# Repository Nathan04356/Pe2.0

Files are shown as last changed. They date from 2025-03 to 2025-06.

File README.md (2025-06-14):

# PE2 - Nathan - Jonas

Wij maakten voor practice enterprise 2 een autonome robot stofzuiger. Deze kan navigeren via infraroodsensoren en een bumper met drukcontacten. Via een drukknop kan de stofzuiger navigeren naar zijn laadstation. Het laadstation is uitgerust met infrarood LEDs waarvan het patroon wordt opgevangen door de IR-receiver op de stofzuiger.

Hardware<br/>
-Schema's en PCB's zijn te vinden onder /Documenten<br/>
-Altium project van zowel stofzuiger als laadstation is terug te vinden in de map /Altium<br/>
-Datasheets zijn per PCB geordend in de map /Datasheets<br/>
Software<br/>
-Code van stofzuiger en laadstation is terug te vinden onder /Documenten<br/>
-STM project van zowel stofzuiger als laadstation is terug te vinden in de map /STM<br/>
Extra<br/>
-Extra info over de IR-sensoren (metingen)<br/>
-Volledige componentenlijst<br/>
Videos<br/>
-Video van gewone werking (stofzuiger.mp4)<br/>
-Video van naar dock te rijden (docking.mp4)<br/>
Verslag en PPT zijn terug te vinden in de root /<br/>

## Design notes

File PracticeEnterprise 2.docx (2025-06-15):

# Practice Enterprise 2:

# Autonome robot stofzuiger

GIT REPO: https://github.com/Nathan04356/PE2.0

# 1. Voorwoord (word of thanks)

Wij willen graag onze dank uiten aan onze leerkrachten die ons zo goed geholpen hebben. Namelijk meneer Dams en meneer Adriaensens.

# 2. Hoe het project gerealiseerd is.

Voor ons project kozen we ervoor om een autonome robotstofzuiger te maken. We begonnen met na te denken over welke functies het toestel moest hebben, zoals zelfstandig kunnen rijden, obstakels vermijden en stof opzuigen. Op basis daarvan besloten we welke onderdelen en modules we nodig hadden.

We maakten eerst een blokschema om een overzicht te krijgen van alle onderdelen en hoe ze met elkaar verbonden moesten worden. Daarna zijn we gestart met het tekenen van het elektrisch schema en het ontwerpen van de printplaat. Dit deden we met behulp van Altium Designer.

Toen de printplaat klaar was, konden we die bestellen en de componenten solderen zodra alles geleverd was.

Voor de programmatie gebruikten we een STM32L053C8T6 microcontroller. We schreven het programma in C, waarbij we de basisfunctionaliteiten van de robot implementeerden, zoals sturen, obstakels detecteren en autonoom bewegen.

# 3. Projectvoorstel

Ons project voorstel is het maken van een autonome robot stofzuiger.

Wij kiezen als centrale punt STM32L053C8T6, die we programeren met STM32CubeProgrammer.

Wij maken 2 PCB’s , één pcb voor de robotsofzuiger en één die als laadstation zal dienen. Wij gebruiken de AU-24.000MBE-T kristal als externe oscillator om een stabiele klok van 24 MHz te voorzien voor de STM32-microcontroller. Voor het programmeren en debuggen gebruiken wij de STLINK-V3MINIE, die via SWD met de microcontroller communiceert.

We gebruiken een lipo batterij van 3.7 v die regelen wij ook naar 3.3 volt om dingen zoals de µcontroller van juiste voeding te voorzien.

Voor de motoren aan te sturen gebruiken we een motor driver (TB6612FNG).

De TB6612FNG stuurt twee DC-motoren aan via een STM32 door per motor de draairichting te bepalen met IN1/IN2 en de snelheid met een PWM-signaal. De driver werkt op 3.3 V logica, heeft een aparte motorvoeding en wordt geactiveerd via de STBY-pin. Ideaal voor compacte, efficiënte robotbesturing.

Wij gebruiken de GP2Y0A21YK0F IR-afstandssensor om obstakels te detecteren. Deze sensor werkt op basis van reflectie van infrarood licht en geeft een analoge spanning die omgekeerd evenredig is met de afstand tot een object. Hij is betrouwbaar voor afstanden tussen ongeveer 10 en 80 cm en wordt via een ADC-ingang van de STM32 uitgelezen. Deze werkt op 5 volt daarmee gebruiken wij een boost converter om van de batterij spanning 3.7v naar 5 v te gaan.

Wij gebruiken eenvoudige mechanische drukcontacten om botsingen te detecteren. Wanneer de voorkant van de robot een obstakel raakt, wordt het contact gesloten en ontvangt de microcontroller een digitaal signaal. Hierdoor kan de robot meteen reageren, bijvoorbeeld door te stoppen of van richting te veranderen. Deze drukcontacten dienen als extra beveiliging naast de IR-sensoren.

Verder willen wij ook een laadstation maken waar de robot stofzuiger zal moeten terug kunnen keren.

Het laadstation maakt gebruik van de BQ24092, een slimme laadchip die een 1-cel Li-ion batterij veilig oplaadt via een standaard 5V micro-USB of VBUS-ingang. Zodra je een oplader aansluit, detecteert de chip dit en laat hij een LED branden via de PG-pin. Als er ook een batterij is aangesloten, start het laadproces en gaat een LED branden via de CHG-pin. Wanneer de batterij volledig is opgeladen, stopt de chip automatisch met laden en gaat de LED uit. De batterij is beschermd tegen overladen en ontladen dankzij een aparte beveiligingschip. Zo zorgt het laadstation automatisch voor veilig en efficiënt opladen.

# 4. Gantt chart

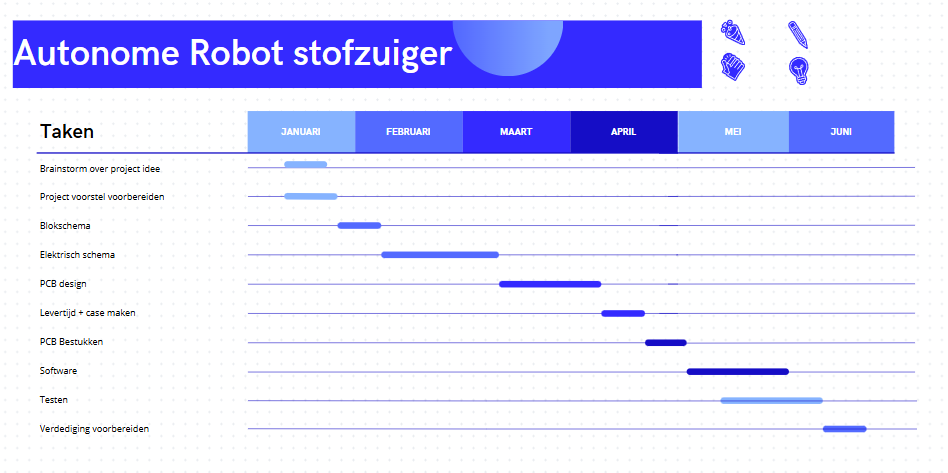
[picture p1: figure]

# 5. Problemen en oplossingen

## 5.1. Voeding

We waren van plan om één 18650-batterij van 3.7V te gebruiken, maar uiteindelijk bleek de stroom die de batterij kan leveren niet hoog genoeg te zijn om de motoren en de stofzuiger tegelijk te laten werken. Hierdoor zijn we moeten overschakelen naar drie batterijen. Als gevolg hiervan is de batterijspanning ook hoger dan de 5V die we nodig hebben voor de IR-sensoren, daardoor hebben we een 5V regelaar gebruikt om de hogere spanning naar 5V te brengen. De boost converter is uit het circuit verwijderd.

## 5.2. Laadstation

Als gevolg van het vorige probleem kan het laadstation niet gebruikt worden omdat het geen drie cellen kan opladen. Het laadstation is wel getest en werkt voor één cel, er zijn contacten voorzien op het station. De contacten op de robotstofzuiger zijn niet voorzien omdat we het laadstation toch niet kunnen gebruiken.

## 5.3. Auto-docking

Op het schema van stofzuiger deel 1 is een spanningsdeler voorzien om het batterijniveau op te meten via de ADC en aan de hand hiervan onder een bepaald niveau terug te rijden naar het station. Deze was uitgerekend voor één cel en is niet meer in gebruik voor drie cellen op dit moment. Weerstand R24 is niet aanwezig op de pcb.

## 5.4. Grond connectie usb

De grond is niet aangesloten op de usb-connector van het laadstation op het schema, waardoor het station eerst geen voeding kreeg. Dit is opgelost door deze aan een naburige grond te solderen.

## 5.5. Polarisatie charge led

De LED op de CHG uitgang van het laadstation staat fout gepolariseerd in het schema, deze is omgedraaid op de pcb.

## 5.6. Boost converter

We gebruikten eerst de TPS61023DRLR boost converter, maar bij het testen bleek dat deze voor kortsluiting zorgde en hebben we deze vervangen door een externe boost converter module. Door het bovenstaand vermelde voedingsprobleem hebben we dan deze module nog een vervangen door een LM7805 regelaar.

# 6. Hardware documentatie

## 6.1 Blokschema

### 6.1.1 Stofzuiger

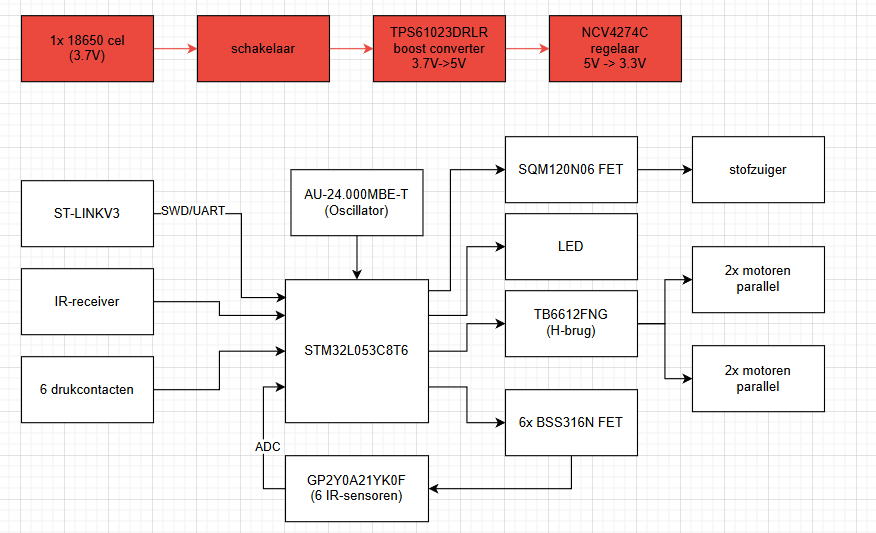
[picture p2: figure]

Het blokschema toont de opbouw van onze autonome robotstofzuiger. Een 3.7 V batterij voedt het systeem via een boost converter en spanningsregelaar. De STM32L053C8T6 microcontroller stuurt de motoren, stofzuiger en LED aan, en ontvangt signalen van IR-sensoren en drukcontacten. Een externe oscillator voorziet een stabiel kloksignaal, en programmering gebeurt via de STLINK-V3MINIE. Alles werkt samen om autonoom te navigeren en obstakels te vermijden.

### 6.1.2 Laadstation

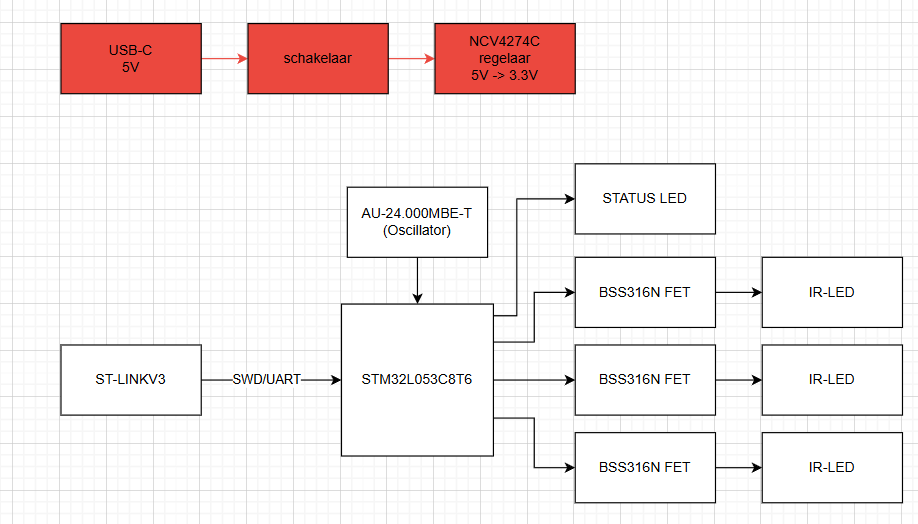
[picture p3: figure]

Dit blokschema toont een vereenvoudeld systeem voor het aansturen van IR-LEDs. De voeding gebeurt via een USB-C aansluiting van 5 V, die via een schakelaar en een NCV4274C spanningsregelaar wordt omgezet naar 3.3 V. De STM32L053C8T6 microcontroller vormt de centrale besturing, aangestuurd door een externe oscillator van 24 MHz. Programmeren gebeurt via ST-LINKV3 via SWD/UART. De microcontroller stuurt drie BSS316N MOSFETs aan die elk een IR-LED schakelen. Daarnaast wordt een status-LED aangestuurd voor visuele feedback.

## 6.2 Schema’s

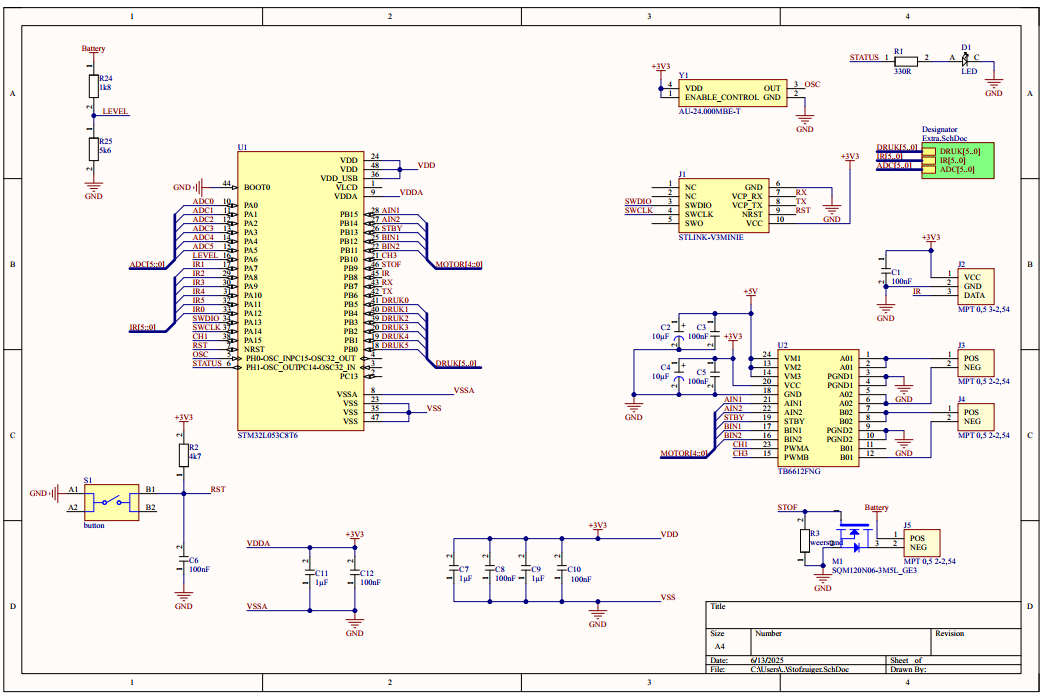
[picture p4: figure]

### 6.2.1 Stofzuiger deel 1

### 6.1.1 Stofzuiger deel 2

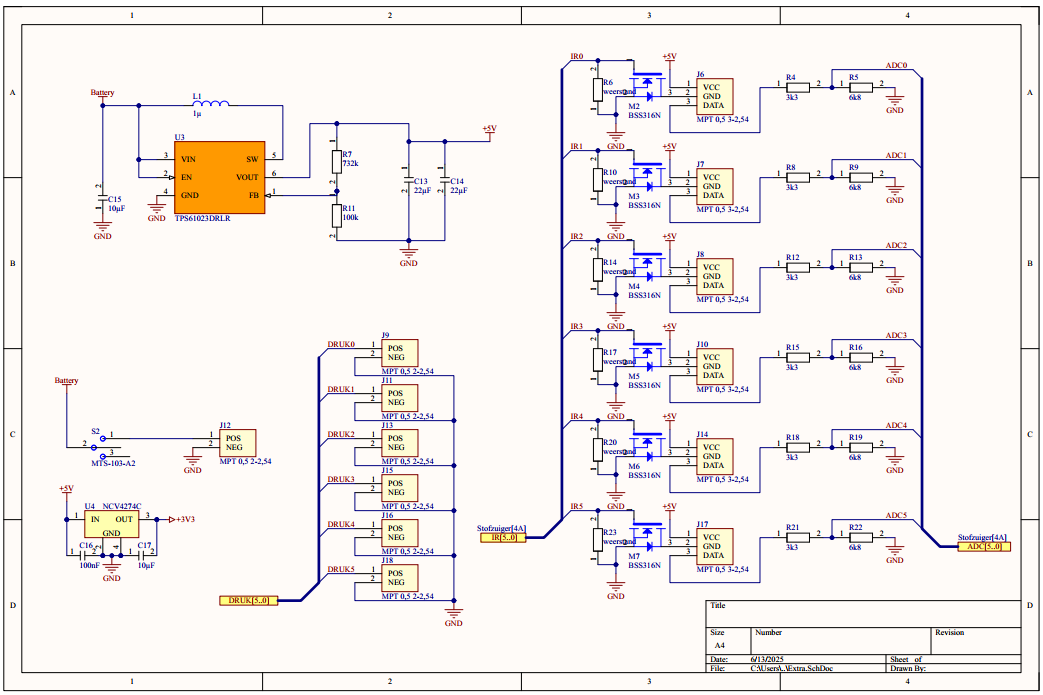
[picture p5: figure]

### 6.1.2 Laadstation deel 1

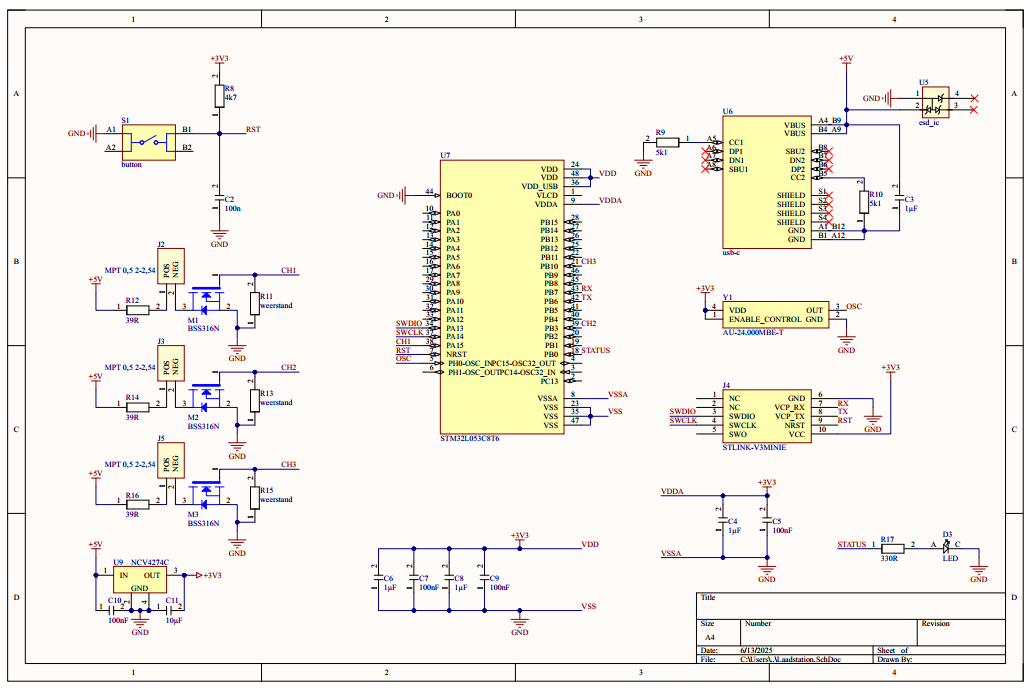
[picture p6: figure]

### 6.1.3 Laadstation deel 2

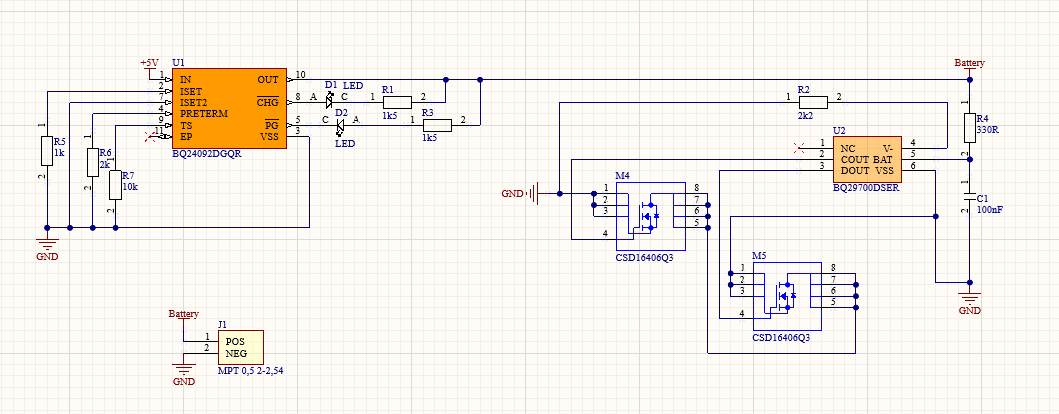
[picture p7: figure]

## 6.1 Component lay-out

### 6.1.1 Stofzuiger top-layer

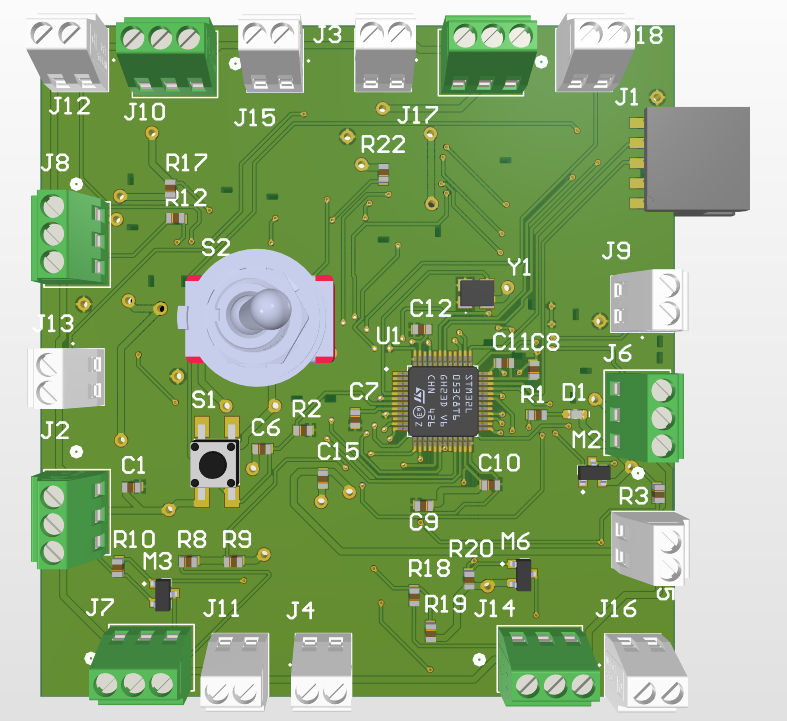
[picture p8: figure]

### 6.1.2 Stofzuiger bottom-layer

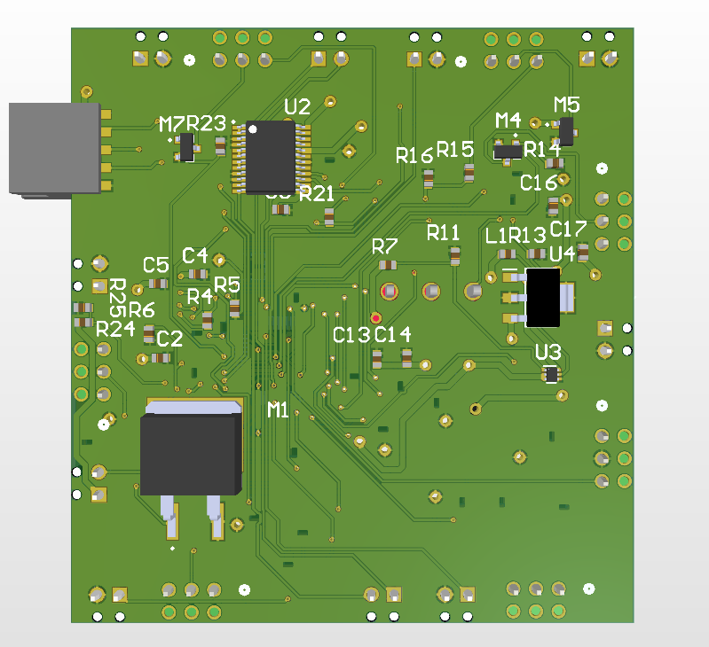
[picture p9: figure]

### 6.1.3 Laadstation

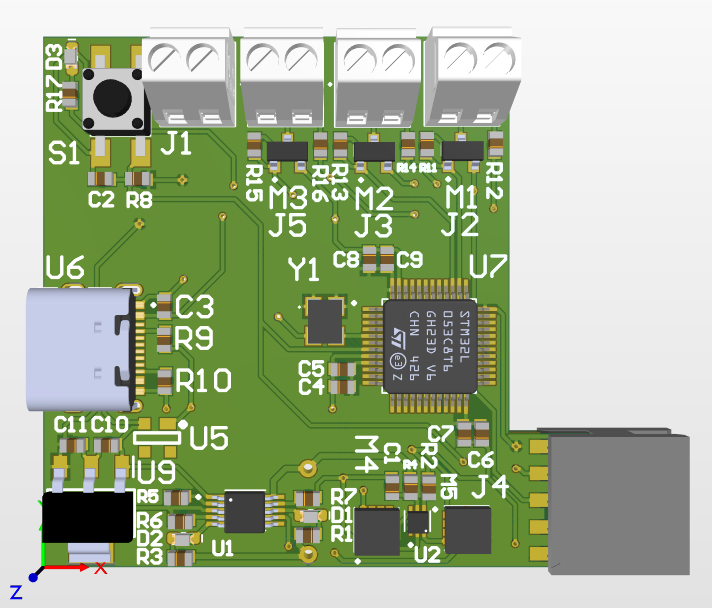
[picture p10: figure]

## 6.2 PCB lay-out

### 6.2.1 Stofzuiger top-layer

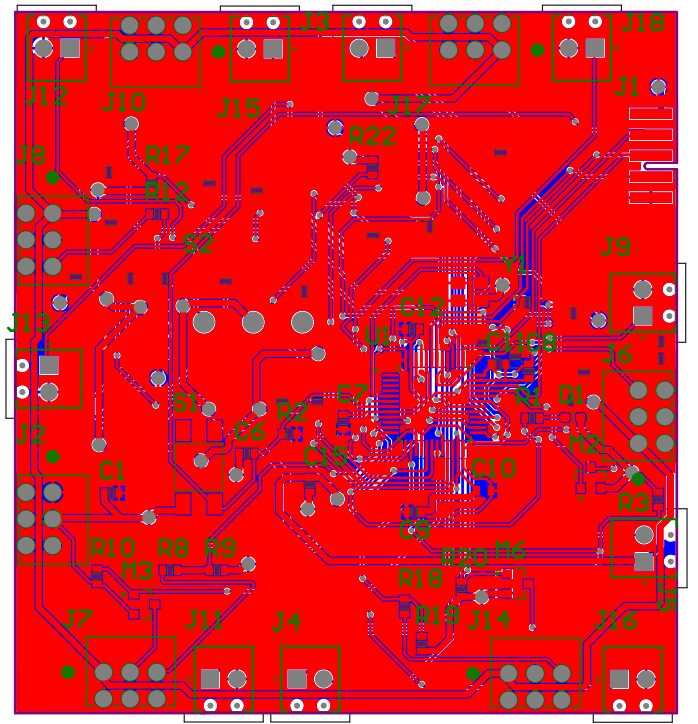
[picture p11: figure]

### 6.2.2 Stofzuiger bottom-layer

### 6.2.3 Laadstation

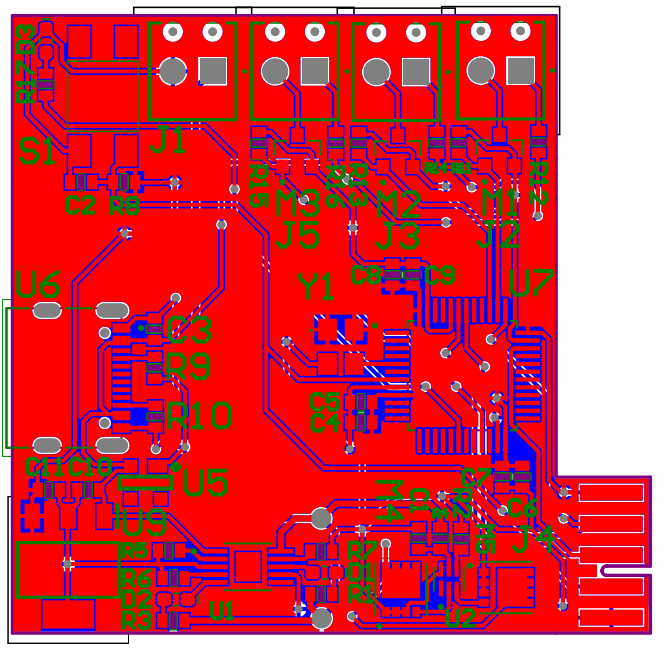
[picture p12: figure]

## 6.3 Materialen

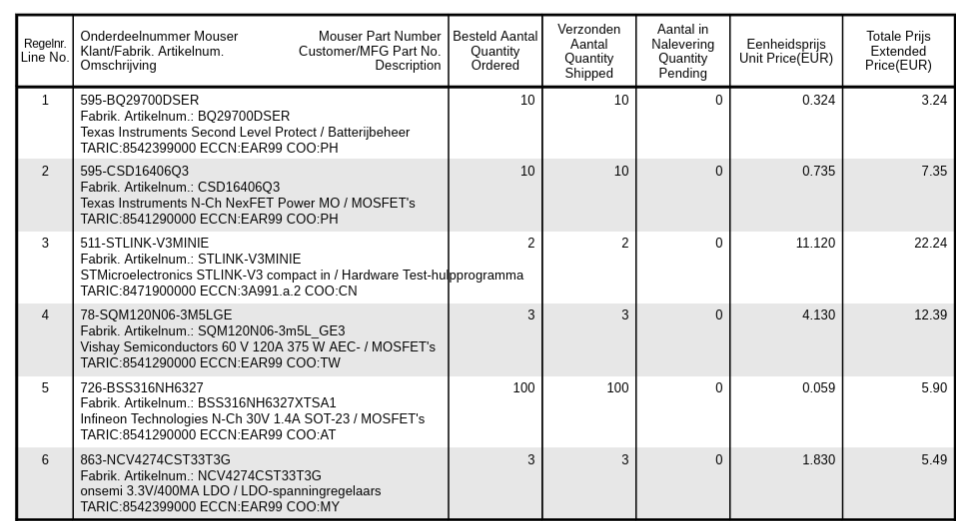
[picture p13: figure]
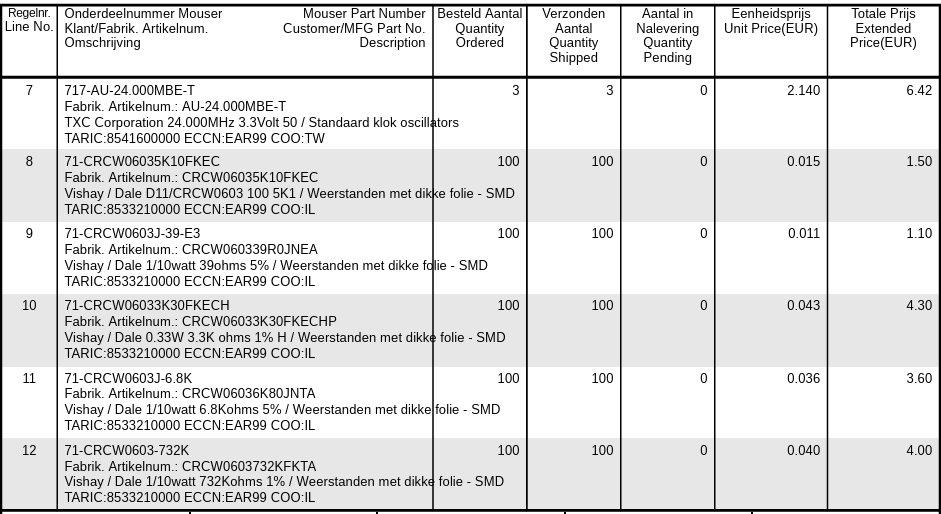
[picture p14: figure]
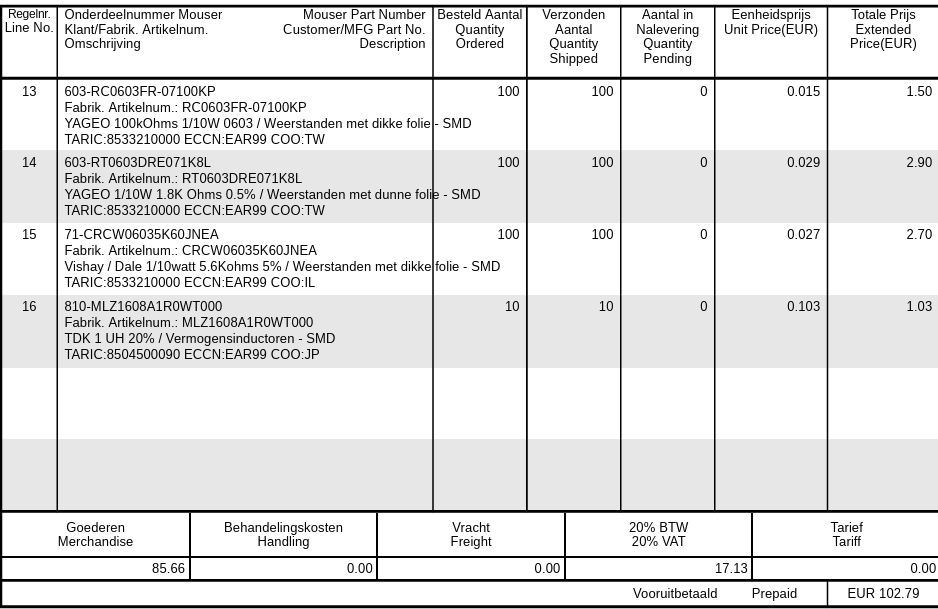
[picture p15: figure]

## 6.4 Datasheets

Datasheet STM32l053c8t6 (https://www.st.com/resource/en/datasheet/stm32l053c8.pdf)

Datasheet TB6612FNG (Dual H-bridge motordriver) (https://toshiba.semicon-storage.com/info/docget.jsp?did=10812&prodName=TB6612FNG)

Datasheet GP2Y0A21YK0F (IR-afstandssensor) (https://global.sharp/products/device/lineup/data/pdf/datasheet/gp2y0a21yk_e.pdf)

Datasheet AU-24.000MBE-T (24 MHz kristaloscillator) (https://abracon.com/Resonators/AU-MBE.pdf)

Datasheet STLINK-V3MINIE (Programmer/debugger) (https://www.st.com/resource/en/user_manual/dm00716816.pdf)

Datasheet Vergelijkbare mechanische drukknop (Omron D2F-type) (https://omronfs.omron.com/en_US/ecb/products/pdf/en-d2f.pdf)

Datasheet SQM120N06-3M5L_GE3 (Mosfet aan uit schakelen stofzuiger)

(https://www.vishay.com/docs/63814/sqm120n06-3m5l.pdf)Datasheet TPS61023DRLR (Boost converter) (https://www.ti.com/lit/ds/symlink/tps61023.pdf)

Datasheet NCV4274C(LDO 3.3 v) (https://www.onsemi.com/pdf/datasheet/ncv4274c-d.pdf)

Datasheet BSS316N (https://www.infineon.com/dgdl/Infineon-BSS316N-DS-v02_03-EN.pdf?fileId=db3a304330f686060130ff7ee4b07f16)

Datasheet BQ24092DGQR (https://www.ti.com/lit/ds/symlink/bq24090.pdf)

Datasheet BQ29700DSER (https://www.ti.com/lit/ds/symlink/bq2970.pdf?ts=1749963523532)

# 7. Software documentatie

## 7.1 Flowchart

### 7.1.1 Stofzuiger

#### 7.1.1.1 Main

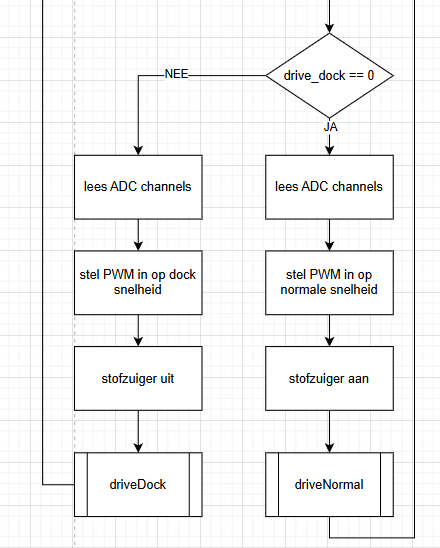
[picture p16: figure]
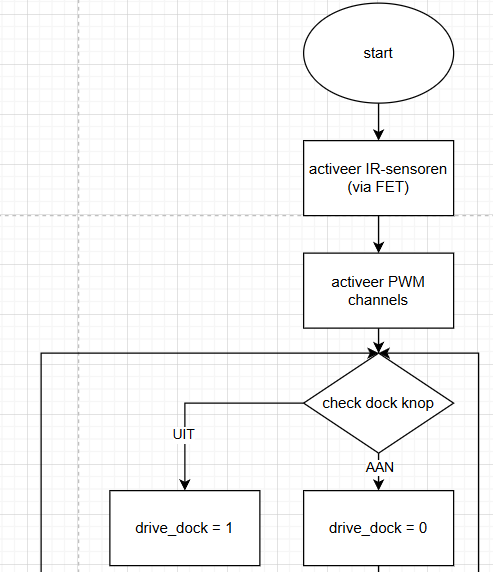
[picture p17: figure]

De stofzuiger zal eerst de nodige IR-sensors activeren en de PWM channels voor de motoren. Hierna wordt de drukknop op de robot gechecked om te beslissen of er naar dock wordt gereden of niet.

Indien de drukknop niet was ingedrukt worden de ADC channels uitgelezen van de IR-sensoren en wordt de PWM op de maximale snelheid ingesteld. De stofzuiger gaat aan en de functie voor het vermijden van opstakels wordt opgeroepen. Als de knop wel was ingedrukt worden de ADC-channels ook gelezen, maar de PWM wordt nu ingesteld op een lagere dock snelheid en de stofzuiger gaat uit.

De 12-bit waarden van de ADC met bijhorende afstand wordt weergeven in volgende grafiek.

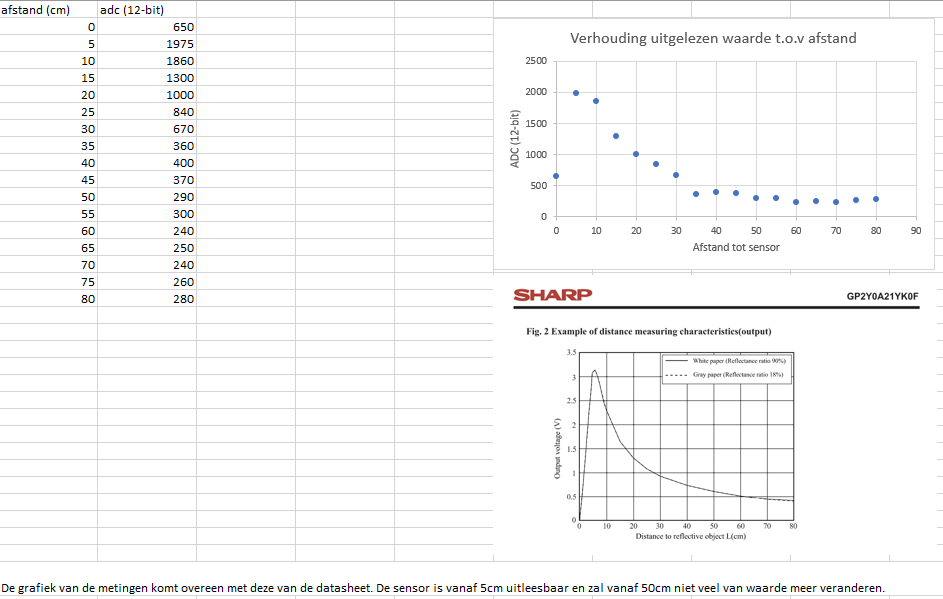
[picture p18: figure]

Hoe groter de ADC-waarde hoe dichter de sensor bij een obstakel is, tenzij te dicht.

#### 7.1.1.2 driveNormal

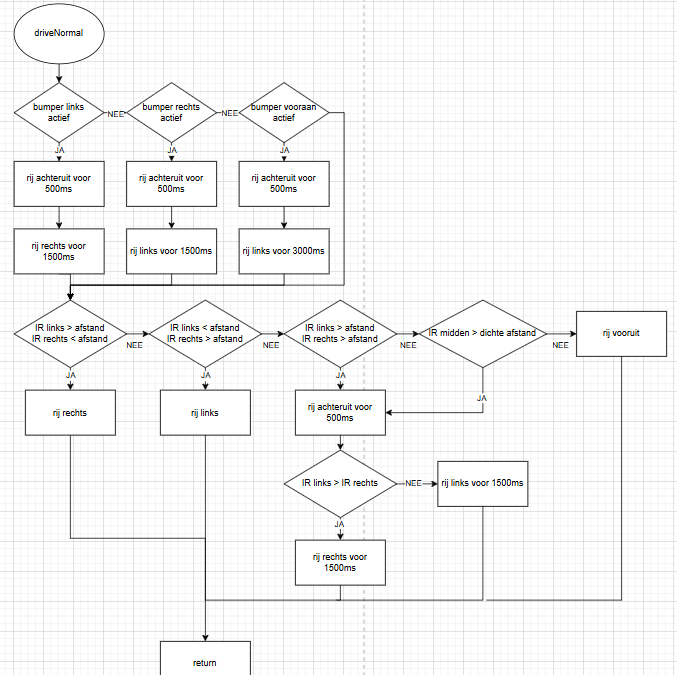
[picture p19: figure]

De obstakel functie bekijkt eerst of er een bumper actief is, indien dit het geval is wordt er achteruitgereden en gedraaid naar de gepaste richting. Daarna worden de afstanden van de IR-sensoren bekeken.

Indien linkse sensor te dicht is wordt er naar rechts gedraaid en omgekeerd bij de rechtse sensor. Als beide links en rechts te dicht zijn of midden veel te dicht wordt er achteruitgereden en afgedraaid naar de kant waar het meeste plaats is. Als geen enkele sensor te dicht komt rijdt de stofzuiger vooruit.

#### 7.1.1.3 driveDock

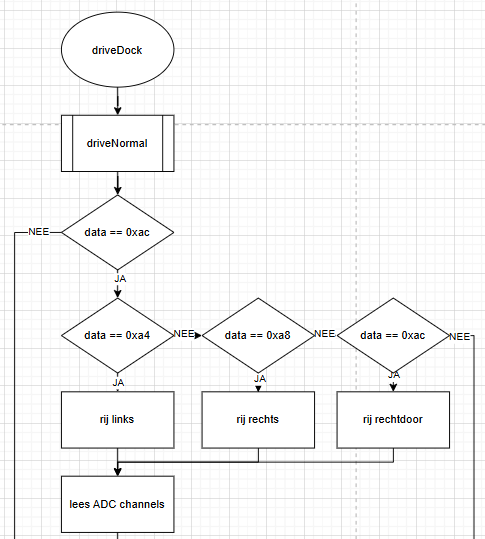
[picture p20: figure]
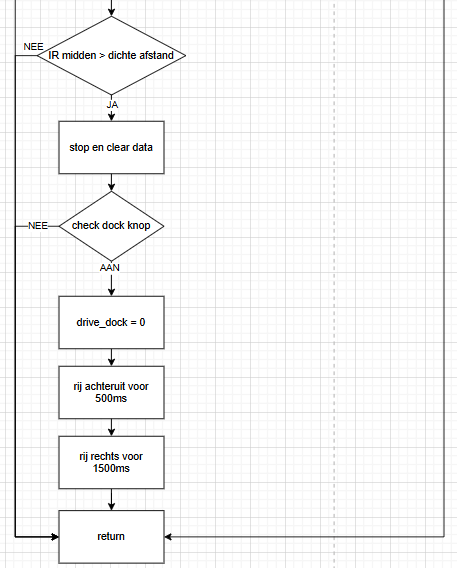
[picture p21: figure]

De ADC-waarden worden gebruikt om te navigeren in de vorig uitgelegde functie driveNormal. De stofzuiger gebruikt dan de data van de IR-receiver (komt vanuit interrupt zie later) om de rechte lijn vanaf het dock station te detecteren.

De linker IR-LED van het dock station stuurt 0xa8 en de rechter 0xa4, samen en dus in het midden is dit 0xac. Indien het midden is gevonden gebruikt de stofzuiger de IR-patronen om te navigeren.

Vervolgens worden de ADC-channels nog gemeten om te checken of de middenste sensor dicht genoeg bij het dock staat. Als deze dicht genoeg is stopt de stofzuiger en wacht deze op een signaal van de dock button. De knop wordt ingedrukt, de stofzuiger rijdt achteruit en naar rechts. Hij gaat terug in de normale modus.

#### 7.1.1.4 interrupt

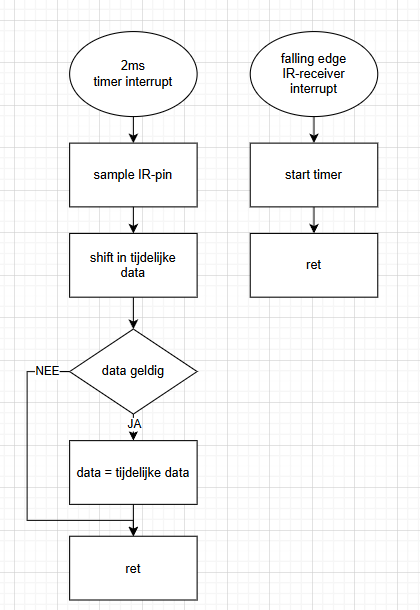
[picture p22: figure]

Het sampelen van de IR-LED data gebeurt via de IR-receiver. Deze geeft een actief laag signaal bij het ontvangen van 38kHz gemoduleerd licht. Er wordt op elke bit gesynchroniseerd door een external interrupt met falling edge detection te gebruiken op de IR-receiver output. Er wordt een timer gestart om in het midden van de bit te sampelen.

De data wordt vervolgens in een tijdelijk register geshift tot er geldige data is en deze beschikbaar is in het gebruikte data register.

### 7.1.2 Laadstation

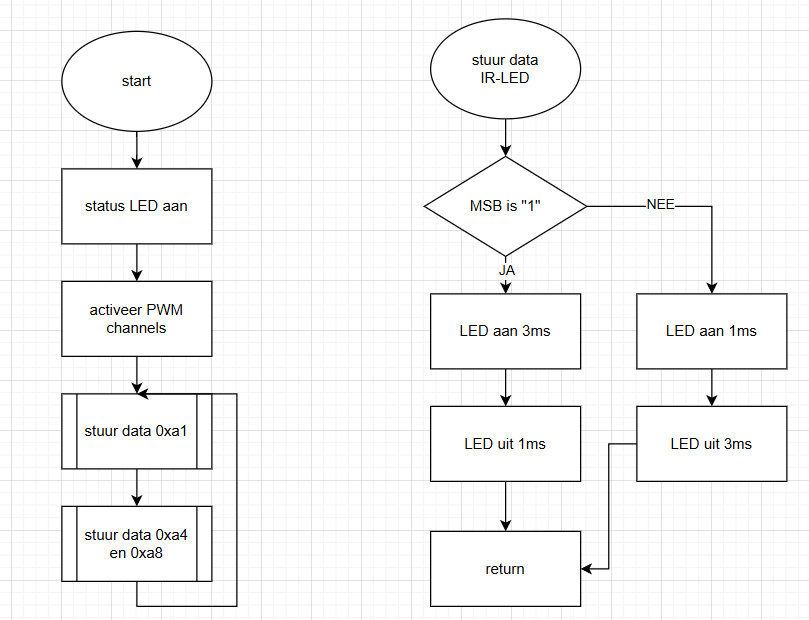
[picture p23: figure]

Het laadstation gebruikt een functie om één channel van een IR-LED op 38kHz te moduleren en data te versturen en een functie om dit te doen op twee channels. Voor de eenvoudigheid is hier rechts de functie voor één channel weergegeven.

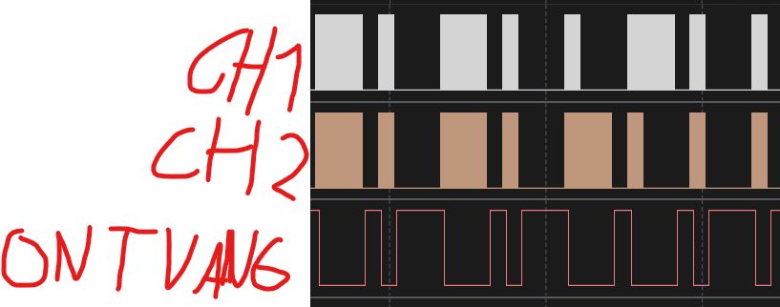
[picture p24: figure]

Indien er een ‘1’ moet worden verstuurd zal de led 3ms aan gaan en 1ms uit. Bij een ‘0’ zal de led 1ms aan gaan en 3ms uit. Hierdoor is er altijd een falling edge op de receiver om te hersynchroniseren. In bovenstaande figuur is CH1 aangestuurd met het patroon 0xa4 en CH2 met 0xa8. Als de ontvanger beide patronen tegelijk ziet komt er 0xac binnen.

# 8. Conclusie

Wij hebben met dit project een autonome robotstofzuiger ontwikkeld die zelfstandig kan navigeren en reageren op zijn omgeving. Door het gebruik van de STM32L053C8T6 microcontroller, IR-afstandssensoren en drukcontacten kan de robot obstakels detecteren en vermijden. De motoren worden efficiënt aangestuurd via een H-brug, en de stofzuigerfunctie wordt afzonderlijk geschakeld. Dankzij een combinatie van hardwareontwerp, printplaatontwikkeling en embedded software zijn we erin geslaagd om een functioneel en uitbreidbaar systeem te realiseren. Dit project heeft ons niet alleen technisch uitgedaagd, maar ook onze samenwerking en probleemoplossend denken versterkt.

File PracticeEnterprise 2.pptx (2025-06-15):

## Robotstofzuiger

Jonas blauwens / nathan vansevenant

## Inhoud

- Blokschema’s
- Schema’s
- PCB’s
- Software
- Problemen
- Conclusie

## Blokschema stofzuiger


## Blokschema laadstation


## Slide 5

Schema stofzuiger deel 1


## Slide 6

Schema stofzuiger deel 2


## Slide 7

Schema laadstation deel 1


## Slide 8

Schema laadstation deel 2


## PCB stofzuiger top


## PCB stofzuiger bottom


## PCB laadstation


## Software stofzuiger


## Software stofzuiger


## Software stofzuiger


## Software IR-LEDS en ontvanger


## Problemen

- Voeding en boost converter
- Opladen
- Auto-docking
- Grond connectie USB
- Polarisatie charge LED
- Boost converter module

## Conclusie


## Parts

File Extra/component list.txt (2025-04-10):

STM32L053C8T6 check 
NCV4274C	spanningsregaal  3.3 v check 3.3
tb6612fng x 3   H-brug check
SHarp GP2Y0A21YK0F x7	IR sensor check  
BQ24092DGQR check
BQ29700DSER check
KW11-3Z-B-1 x 10 botssesnor check 
micro N20 gear motor niet meer nodig
Phoenix contact x2 x10 check
Phoenix contact x3 x14 check genoeg?

STLINK-V3MINIE check

led check

SQM120N06-3M5L_GE3 check 
BSS316N check
MTS-103-A2 check
TB6612FNG check
TPS61023DRLR check
NCV4274C check
AU-24.000MBE-T check
CSD16406Q3 check
BQ24092DGQR check
BQ29700DSER check
esd_ic check
usb-c check

100nF check

22µF check
10µF check

100nF check
100n check
1µF check

3k3 check
6k8 check
732k check
100k check
1k8 check
5k6 check

spoel 1µ check

1k5 check
2k2 check
330R check
1k check
2k check
10k check
4k7 check 
5k1 check
39R check

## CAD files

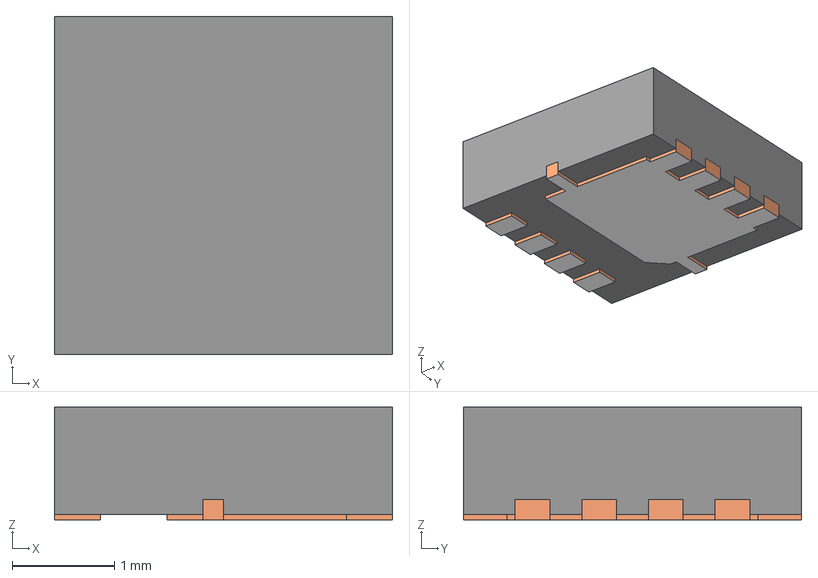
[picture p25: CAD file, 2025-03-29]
Altium/PE2/3D modellen/DQG0008A.stp
3.30 x 3.30 x 1.10 mm
BODY-SON
FRAME-DQG0008A
PIN1-ID

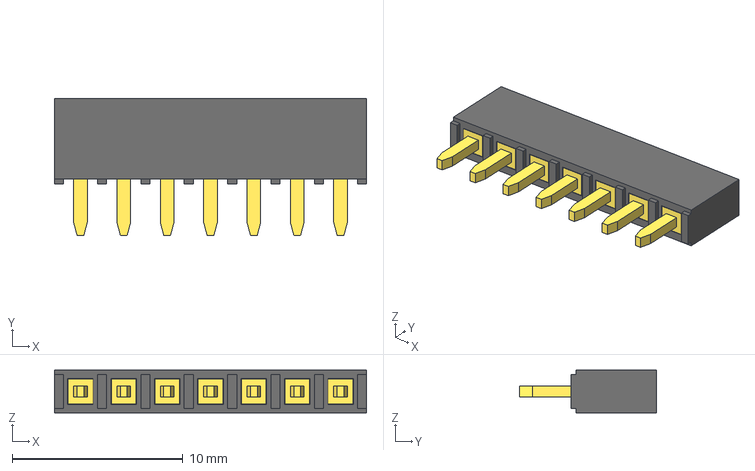
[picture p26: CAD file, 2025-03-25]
Altium/PE2/3D modellen/7-Pin Header - Female - 2.54mm.step
18.3 x 8.00 x 2.50 mm

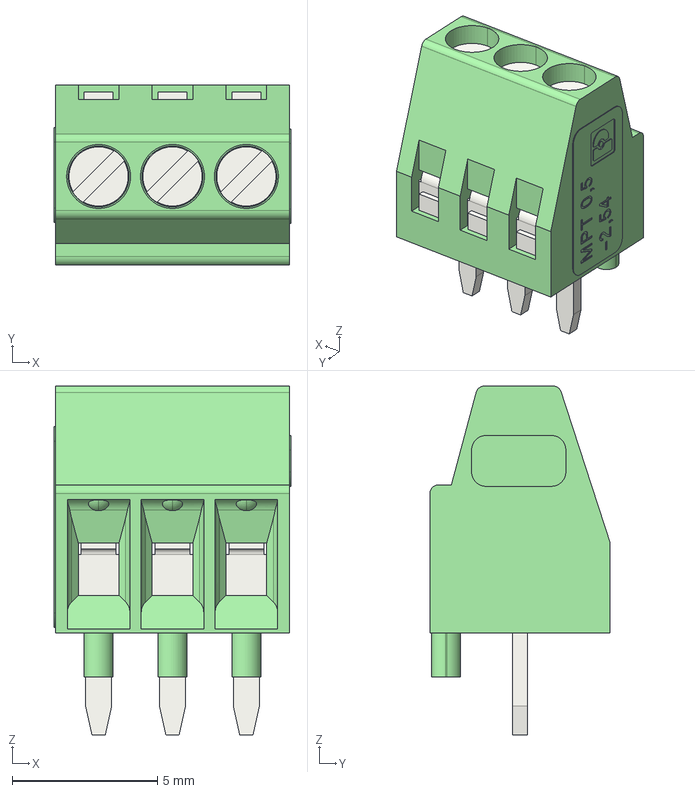
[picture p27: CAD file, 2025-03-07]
Altium/PE2/3D modellen/pxc_1725669_09_03_MPT-0-5-3-2-54_3D.stp
8.14 x 6.20 x 12.0 mm

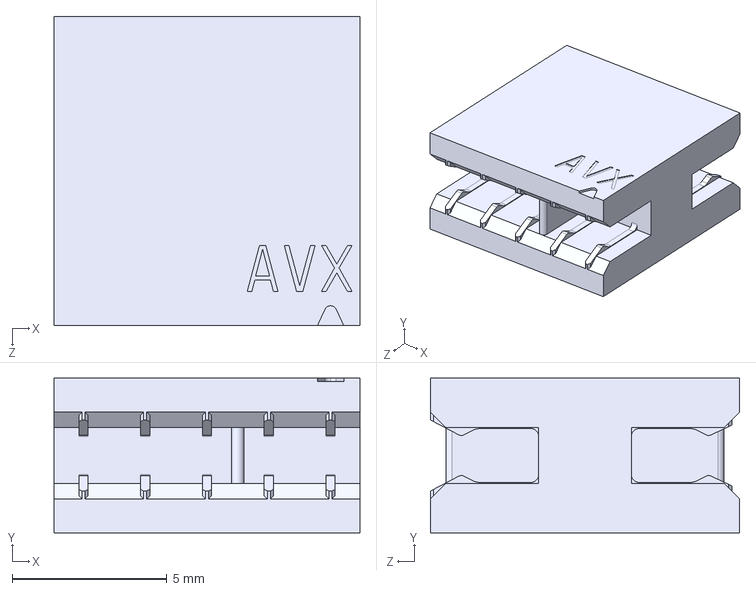
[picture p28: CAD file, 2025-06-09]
Altium/PE2/3D modellen/009159010061916.stp
9.90 x 5.00 x 10.0 mm

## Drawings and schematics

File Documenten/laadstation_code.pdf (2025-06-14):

main.c | Saturday, June 14, 2025, 2:55 PM

1 /* USER CODE BEGIN Header */
2 /**
3 ******************************************************************************
4 | * @file | : main.c
5 | * @brief | : Main program body
6 ****************************************************************************** 7 * @attention
8 *
9 * Copyright (c) 2025 STMicroelectronics.
10 * All rights reserved.
11 *
12 * This software is licensed under terms that can be found in the LICENSE file 13 * in the root directory of this software component.
14 * If no LICENSE file comes with this software, it is provided AS-IS.
15 *
16 ****************************************************************************** 17 */
18 /* USER CODE END Header */
19 /* Includes ------------------------------------------------------------------*/ 20 #include "main.h"
21
22 /* Private includes ----------------------------------------------------------*/ 23 /* USER CODE BEGIN Includes */
24 #include <stdio.h>
25 /* USER CODE END Includes */
26
27 /* Private typedef -----------------------------------------------------------*/ 28 /* USER CODE BEGIN PTD */
29
30 /* USER CODE END PTD */
31
32 /* Private define ------------------------------------------------------------*/ 33 /* USER CODE BEGIN PD */
34
35 /* USER CODE END PD */
36
37 /* Private macro -------------------------------------------------------------*/ 38 /* USER CODE BEGIN PM */
39 #define DUTY_VAL 14
40 /* USER CODE END PM */
41
42 /* Private variables ---------------------------------------------------------*/ 43 TIM_HandleTypeDef htim2;
44
45 UART_HandleTypeDef huart1;
46
47 /* USER CODE BEGIN PV */ 48
49 /* USER CODE END PV */
50
51 /* Private function prototypes -----------------------------------------------*/ 52 void SystemClock_Config(void);
53 static void MX_GPIO_Init(void);
54 static void MX_USART1_UART_Init(void);
55 static void MX_TIM2_Init(void);
56 /* USER CODE BEGIN PFP */
57 int _write(int, char *, int);
58 void stuurDataIrSolo (uint8_t);
59 void stuurDataIrDuo (uint8_t, uint8_t);
60 void stuurDataIrAll (uint8_t, uint8_t, uint8_t);
61 /* USER CODE END PFP */
62
63 /* Private user code ---------------------------------------------------------*/ 64 /* USER CODE BEGIN 0 */
| | Page 1

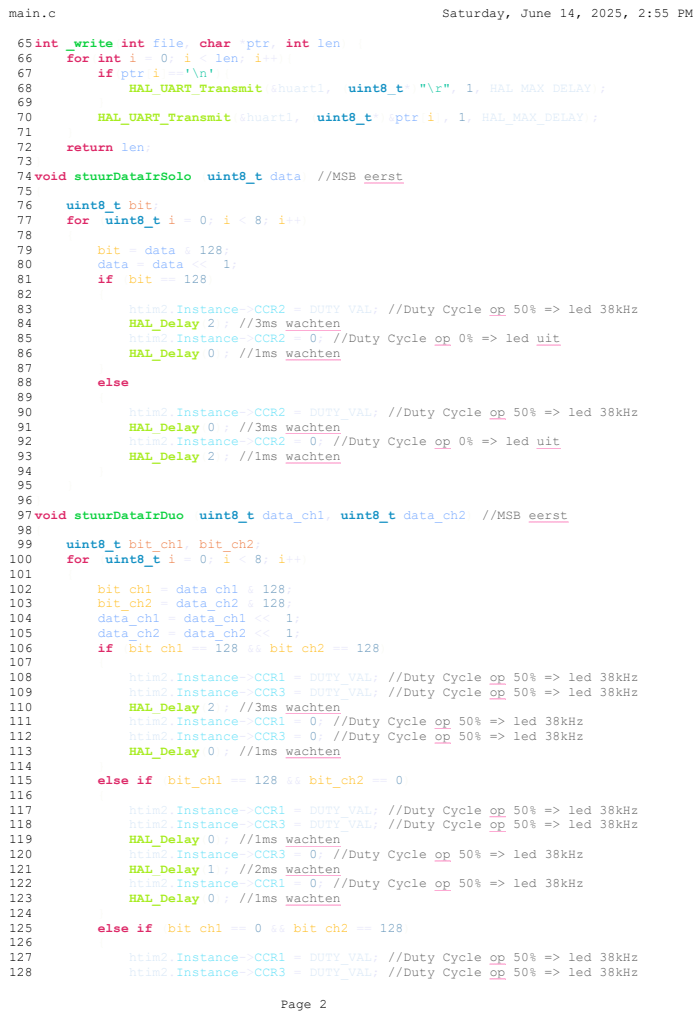
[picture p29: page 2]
main.c; Saturday, June 14, 2025, 2:55 PM; Page 2

65 int _write(int file, char *ptr, int len) {
66 for(int i = 0; i < len; i++){
67 if(ptr[i]=='\n'){
68 HAL_UART_Transmit(&huart1, (uint8_t*)"\r", 1, HAL_MAX_DELAY);
70 HAL_UART_Transmit(&huart1, (uint8_t*)&ptr[i], 1, HAL_MAX_DELAY);
72 return len;
74 void stuurDataIrSolo (uint8_t data) //MSB eerst
76 uint8_t bit;
77 for (uint8_t i = 0; i < 8; i++)
79 bit = data & 128;
80 data = data << 1;
81 if (bit == 128)
83 htim2.Instance->CCR2 = DUTY_VAL; //Duty Cycle op 50% => led 38kHz
84 HAL_Delay(2); //3ms wachten
85 htim2.Instance->CCR2 = 0; //Duty Cycle op 0% => led uit
86 HAL_Delay(0); //1ms wachten
88 else
90 htim2.Instance->CCR2 = DUTY_VAL; //Duty Cycle op 50% => led 38kHz
91 HAL_Delay(0); //3ms wachten
92 htim2.Instance->CCR2 = 0; //Duty Cycle op 0% => led uit
93 HAL_Delay(2); //1ms wachten
97 void stuurDataIrDuo (uint8_t data_ch1, uint8_t data_ch2) //MSB eerst
99 uint8_t bit_ch1, bit_ch2;
100 for (uint8_t i = 0; i < 8; i++)
102 bit_ch1 = data_ch1 & 128;
103 bit_ch2 = data_ch2 & 128;
104 data_ch1 = data_ch1 << 1;
105 data_ch2 = data_ch2 << 1;
106 if (bit_ch1 == 128 && bit_ch2 == 128)
108 htim2.Instance->CCR1 = DUTY_VAL; //Duty Cycle op 50% => led 38kHz
109 htim2.Instance->CCR3 = DUTY_VAL; //Duty Cycle op 50% => led 38kHz
110 HAL_Delay(2); //3ms wachten
111 htim2.Instance->CCR1 = 0; //Duty Cycle op 50% => led 38kHz
112 htim2.Instance->CCR3 = 0; //Duty Cycle op 50% => led 38kHz
113 HAL_Delay(0); //1ms wachten
115 else if (bit_ch1 == 128 && bit_ch2 == 0)
117 htim2.Instance->CCR1 = DUTY_VAL; //Duty Cycle op 50% => led 38kHz
118 htim2.Instance->CCR3 = DUTY_VAL; //Duty Cycle op 50% => led 38kHz
119 HAL_Delay(0); //1ms wachten
120 htim2.Instance->CCR3 = 0; //Duty Cycle op 50% => led 38kHz
121 HAL_Delay(1); //2ms wachten
122 htim2.Instance->CCR1 = 0; //Duty Cycle op 50% => led 38kHz
123 HAL_Delay(0); //1ms wachten
125 else if (bit_ch1 == 0 && bit_ch2 == 128)
127 htim2.Instance->CCR1 = DUTY_VAL; //Duty Cycle op 50% => led 38kHz
128 htim2.Instance->CCR3 = DUTY_VAL; //Duty Cycle op 50% => led 38kHz

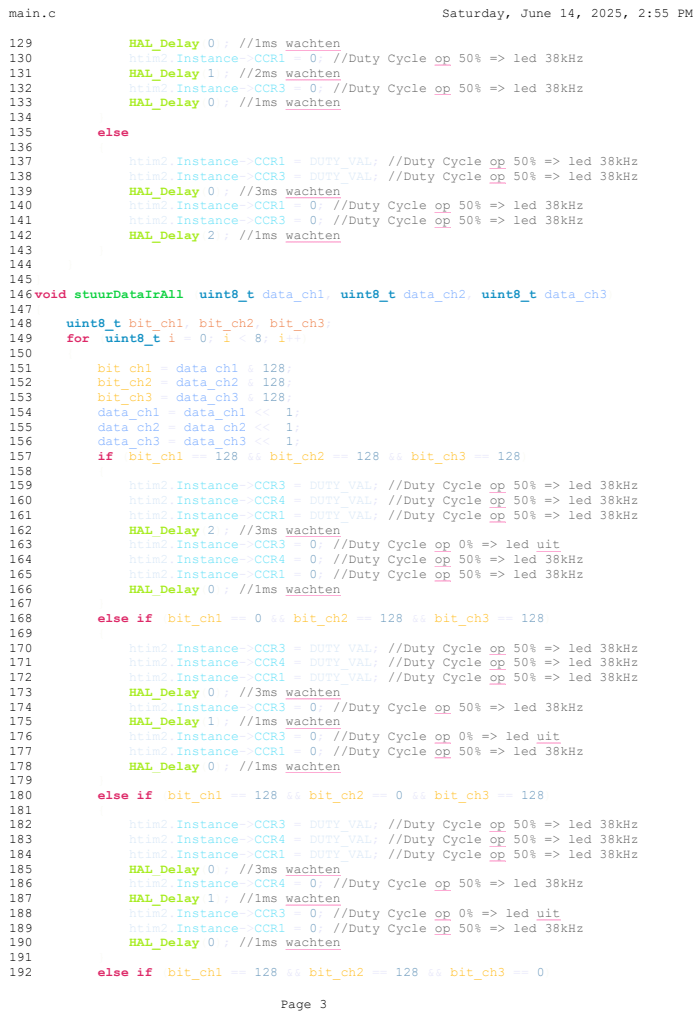
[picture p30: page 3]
main.c; Saturday, June 14, 2025, 2:55 PM; Page 3
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

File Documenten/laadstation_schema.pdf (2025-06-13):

4k7 2 1

# GND 2 1

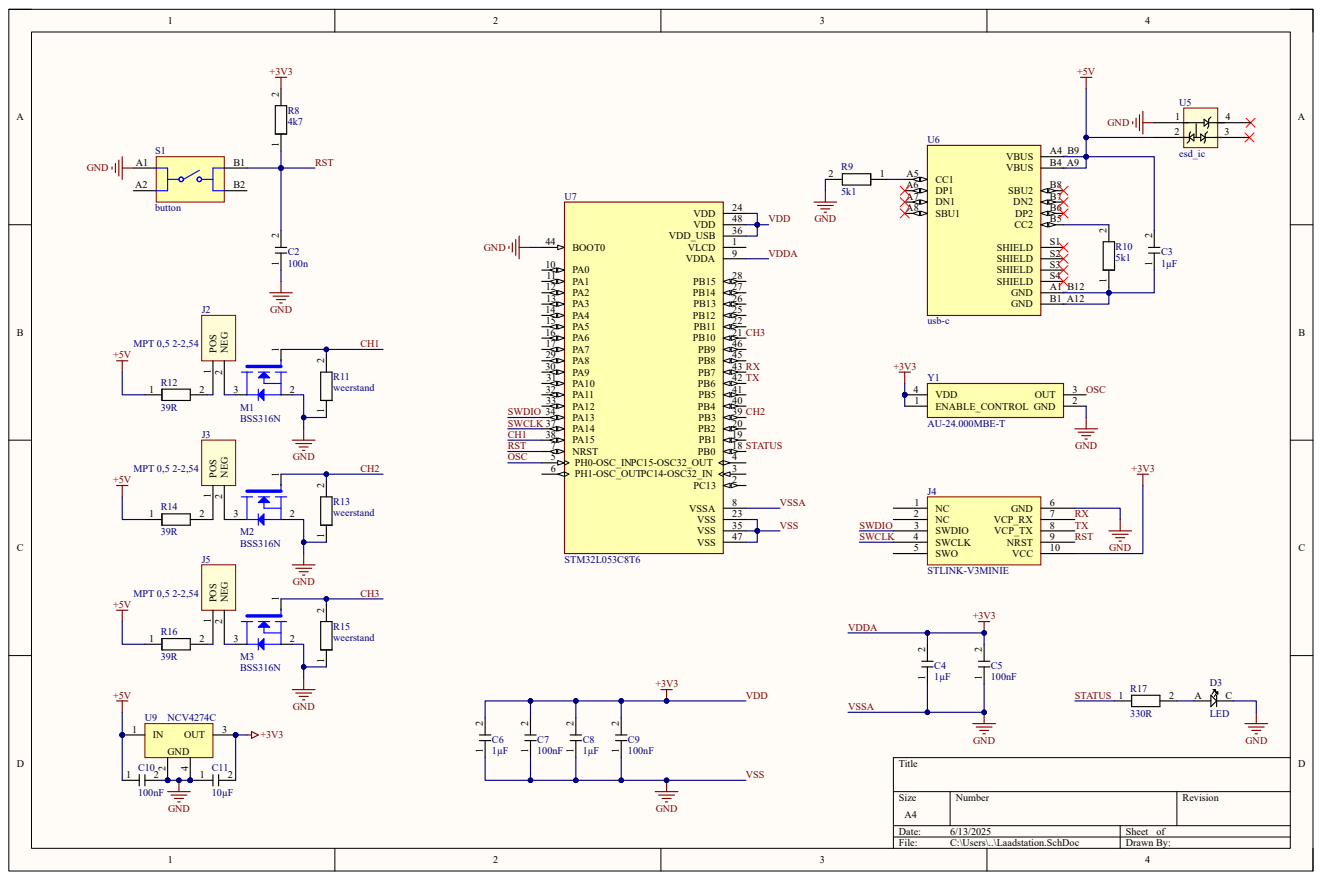
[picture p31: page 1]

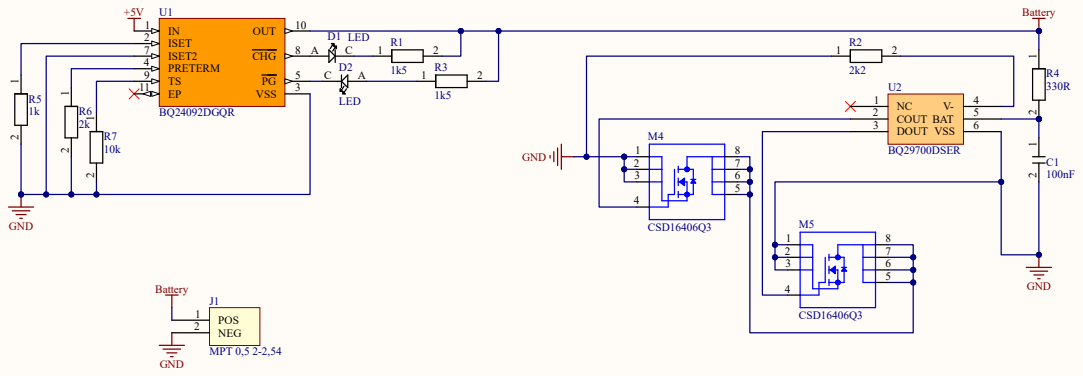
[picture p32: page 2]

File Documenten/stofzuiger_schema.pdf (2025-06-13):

IR[5..0] 2 1

1k8 1 2

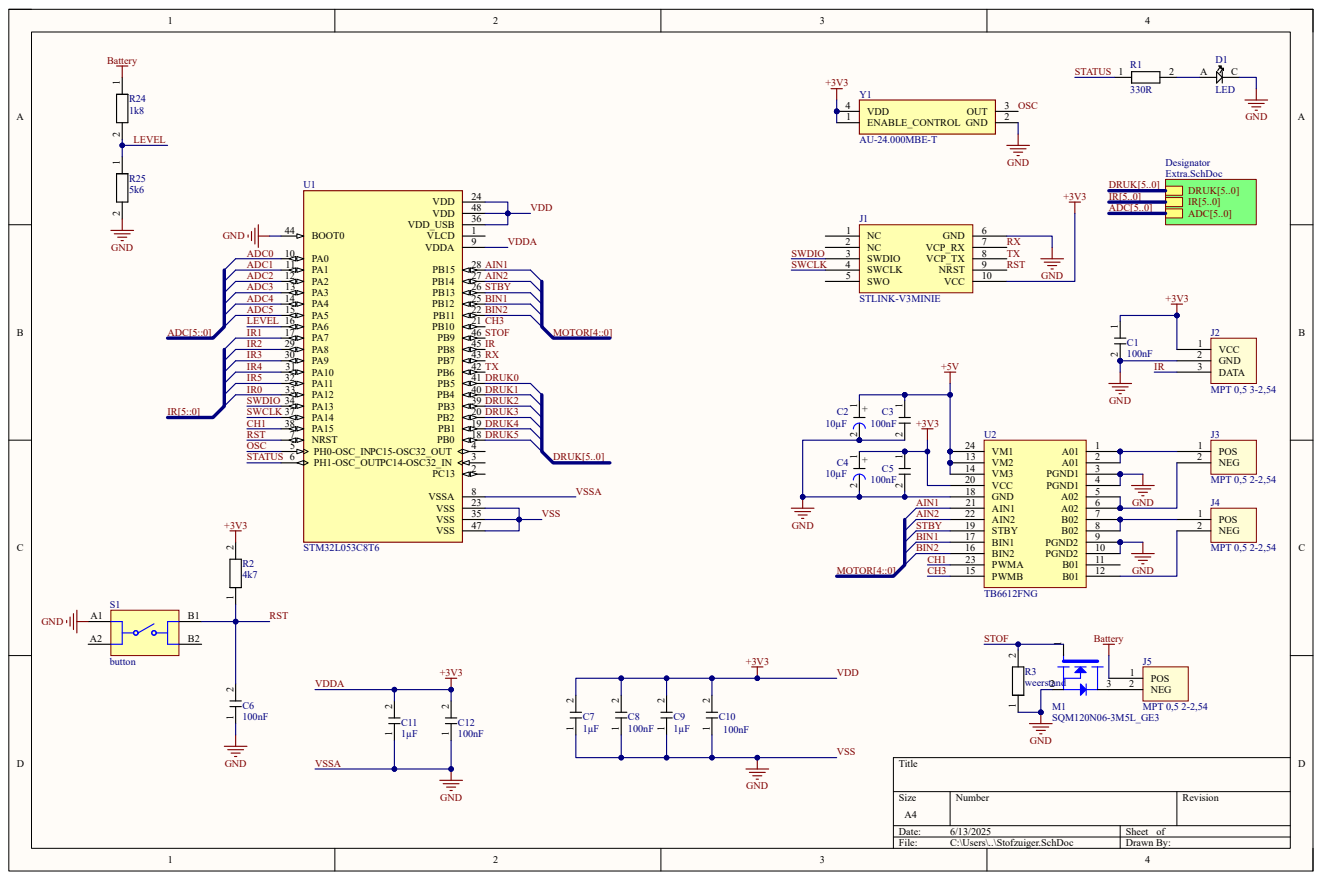
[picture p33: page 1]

732k 1 2

# GND ¹ 2

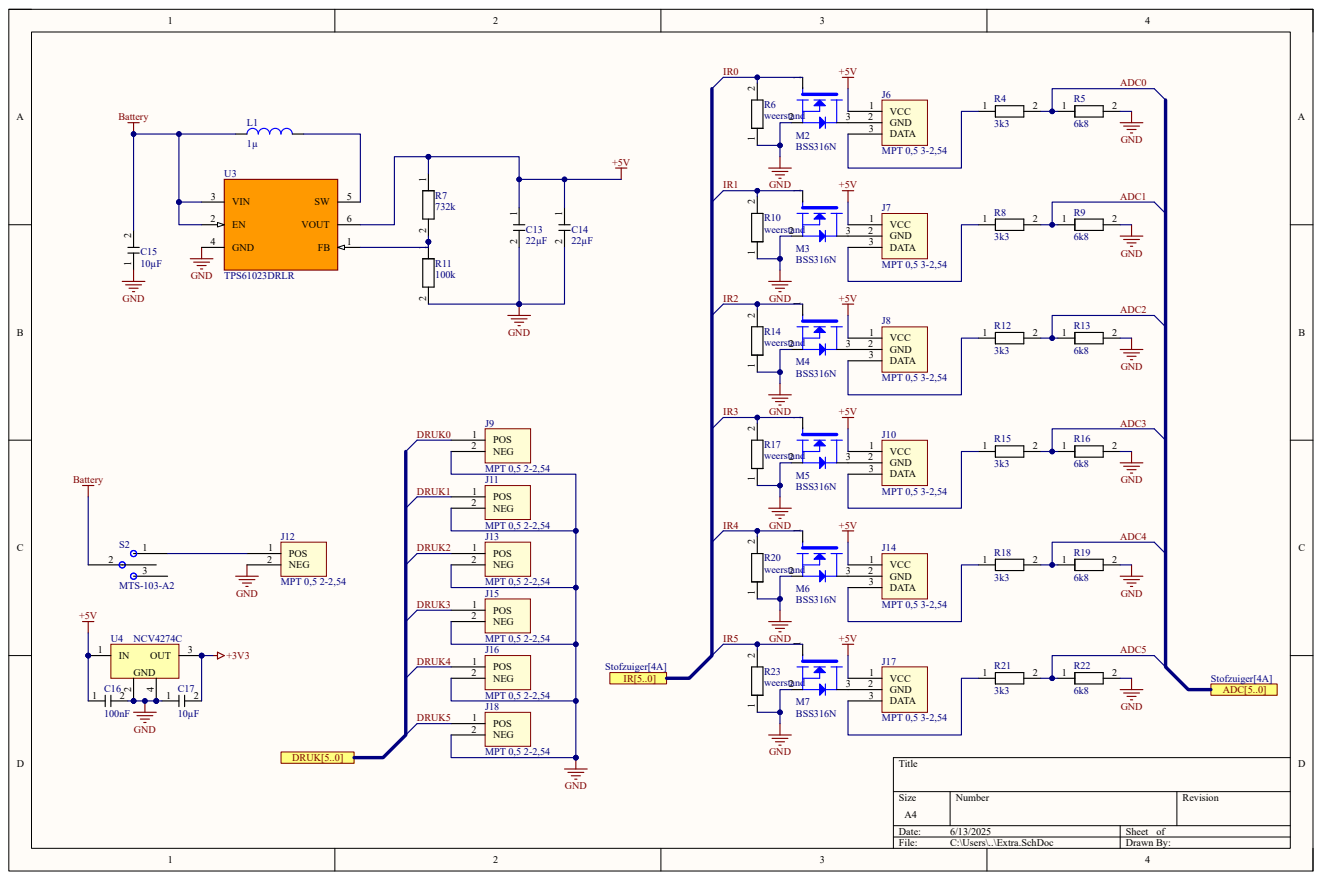
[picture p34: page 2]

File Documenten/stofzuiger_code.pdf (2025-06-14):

main.c | Saturday, June 14, 2025, 2:54 PM

1 /* USER CODE BEGIN Header */
2 /**
3 ******************************************************************************
4 | * @file | : main.c
5 | * @brief | : Main program body
6 ****************************************************************************** 7 * @attention
8 *
9 * Copyright (c) 2025 STMicroelectronics.
10 * All rights reserved.
11 *
12 * This software is licensed under terms that can be found in the LICENSE file 13 * in the root directory of this software component.
14 * If no LICENSE file comes with this software, it is provided AS-IS.
15 *
16 ****************************************************************************** 17 */
18 /* USER CODE END Header */
19 /* Includes ------------------------------------------------------------------*/ 20 #include "main.h"
21
22 /* Private includes ----------------------------------------------------------*/ 23 /* USER CODE BEGIN Includes */
24 #include <stdio.h>
25 /* USER CODE END Includes */
26
27 /* Private typedef -----------------------------------------------------------*/ 28 /* USER CODE BEGIN PTD */
29
30 /* USER CODE END PTD */
31
32 /* Private define ------------------------------------------------------------*/ 33 /* USER CODE BEGIN PD */
34
35 /* USER CODE END PD */
36
37 /* Private macro -------------------------------------------------------------*/ 38 /* USER CODE BEGIN PM */
39 #define VOORUIT (GPIOB->BSRR = 0xF800B000);
40 #define ACHTERUIT (GPIOB->BSRR = 0xF8006800);
41 #define LINKS (GPIOB->BSRR = 0xF800A800);
42 #define RECHTS (GPIOB->BSRR = 0xF8007000); 43 #define UIT (GPIOB->BSRR = 0xF8000000);
44 #define NORMAL_SPEED 255
45 #define DOCK_SPEED 145
46 #define IR_SENSOR_COUNT 3
47 #define IR_SENSOR_DISTANCE 1500
48 #define IR_MID_SENSOR_DISTANCE 2200 49 #define ACHTERUIT_DELAY 500
50 #define DRAAI_DELAY 1500
51 #define LANG_DRAAI_DELAY 3000
52 /* USER CODE END PM */
53
54 /* Private variables ---------------------------------------------------------*/ 55 ADC_HandleTypeDef hadc;
56
57 TIM_HandleTypeDef htim2;
58 TIM_HandleTypeDef htim6; 59
60 UART_HandleTypeDef huart1; 61
62 /* USER CODE BEGIN PV */ 63 uint8_t sample = 0;
64 uint8_t data = 0;
| | Page 1

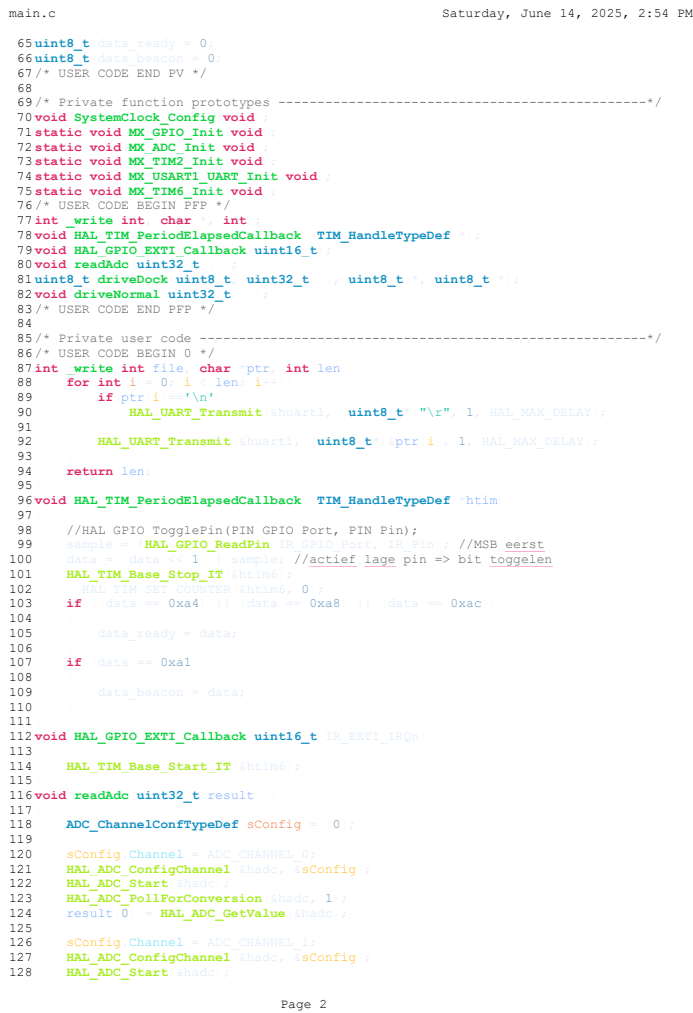
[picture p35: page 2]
main.c; Saturday, June 14, 2025, 2:54 PM; Page 2

65 uint8_t data_ready = 0;
66 uint8_t data_beacon = 0;
67 /* USER CODE END PV */
69 /* Private function prototypes -----------------------------------------------*/
70 void SystemClock_Config(void);
71 static void MX_GPIO_Init(void);
72 static void MX_ADC_Init(void);
73 static void MX_TIM2_Init(void);
74 static void MX_USART1_UART_Init(void);
75 static void MX_TIM6_Init(void);
76 /* USER CODE BEGIN PFP */
77 int _write(int, char *, int);
78 void HAL_TIM_PeriodElapsedCallback (TIM_HandleTypeDef *);
79 void HAL_GPIO_EXTI_Callback(uint16_t);
80 void readAdc(uint32_t []);
81 uint8_t driveDock(uint8_t, uint32_t [], uint8_t *, uint8_t *);
82 void driveNormal(uint32_t []);
83 /* USER CODE END PFP */
85 /* Private user code ---------------------------------------------------------*/
86 /* USER CODE BEGIN 0 */
87 int _write(int file, char *ptr, int len) {
88 for(int i = 0; i < len; i++){
89 if(ptr[i]=='\n'){
90 HAL_UART_Transmit(&huart1, (uint8_t*)"\r", 1, HAL_MAX_DELAY);
92 HAL_UART_Transmit(&huart1, (uint8_t*)&ptr[i], 1, HAL_MAX_DELAY);
94 return len;
96 void HAL_TIM_PeriodElapsedCallback (TIM_HandleTypeDef *htim)
98 //HAL_GPIO_TogglePin(PIN_GPIO_Port, PIN_Pin);
99 sample = !HAL_GPIO_ReadPin(IR_GPIO_Port, IR_Pin); //MSB eerst
100 data = (data << 1) | sample; //actief lage pin => bit toggelen
101 HAL_TIM_Base_Stop_IT(&htim6);
102 __HAL_TIM_SET_COUNTER(&htim6, 0);
103 if ((data == 0xa4) || (data == 0xa8) || (data == 0xac))
105 data_ready = data;
107 if (data == 0xa1)
109 data_beacon = data;
112 void HAL_GPIO_EXTI_Callback(uint16_t IR_EXTI_IRQn)
114 HAL_TIM_Base_Start_IT(&htim6);
116 void readAdc(uint32_t result[])
118 ADC_ChannelConfTypeDef sConfig = {0};
120 sConfig.Channel = ADC_CHANNEL_0;
121 HAL_ADC_ConfigChannel(&hadc, &sConfig);
122 HAL_ADC_Start(&hadc);
123 HAL_ADC_PollForConversion(&hadc, 1);
124 result[0] = HAL_ADC_GetValue(&hadc);
126 sConfig.Channel = ADC_CHANNEL_1;
127 HAL_ADC_ConfigChannel(&hadc, &sConfig);
128 HAL_ADC_Start(&hadc);
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

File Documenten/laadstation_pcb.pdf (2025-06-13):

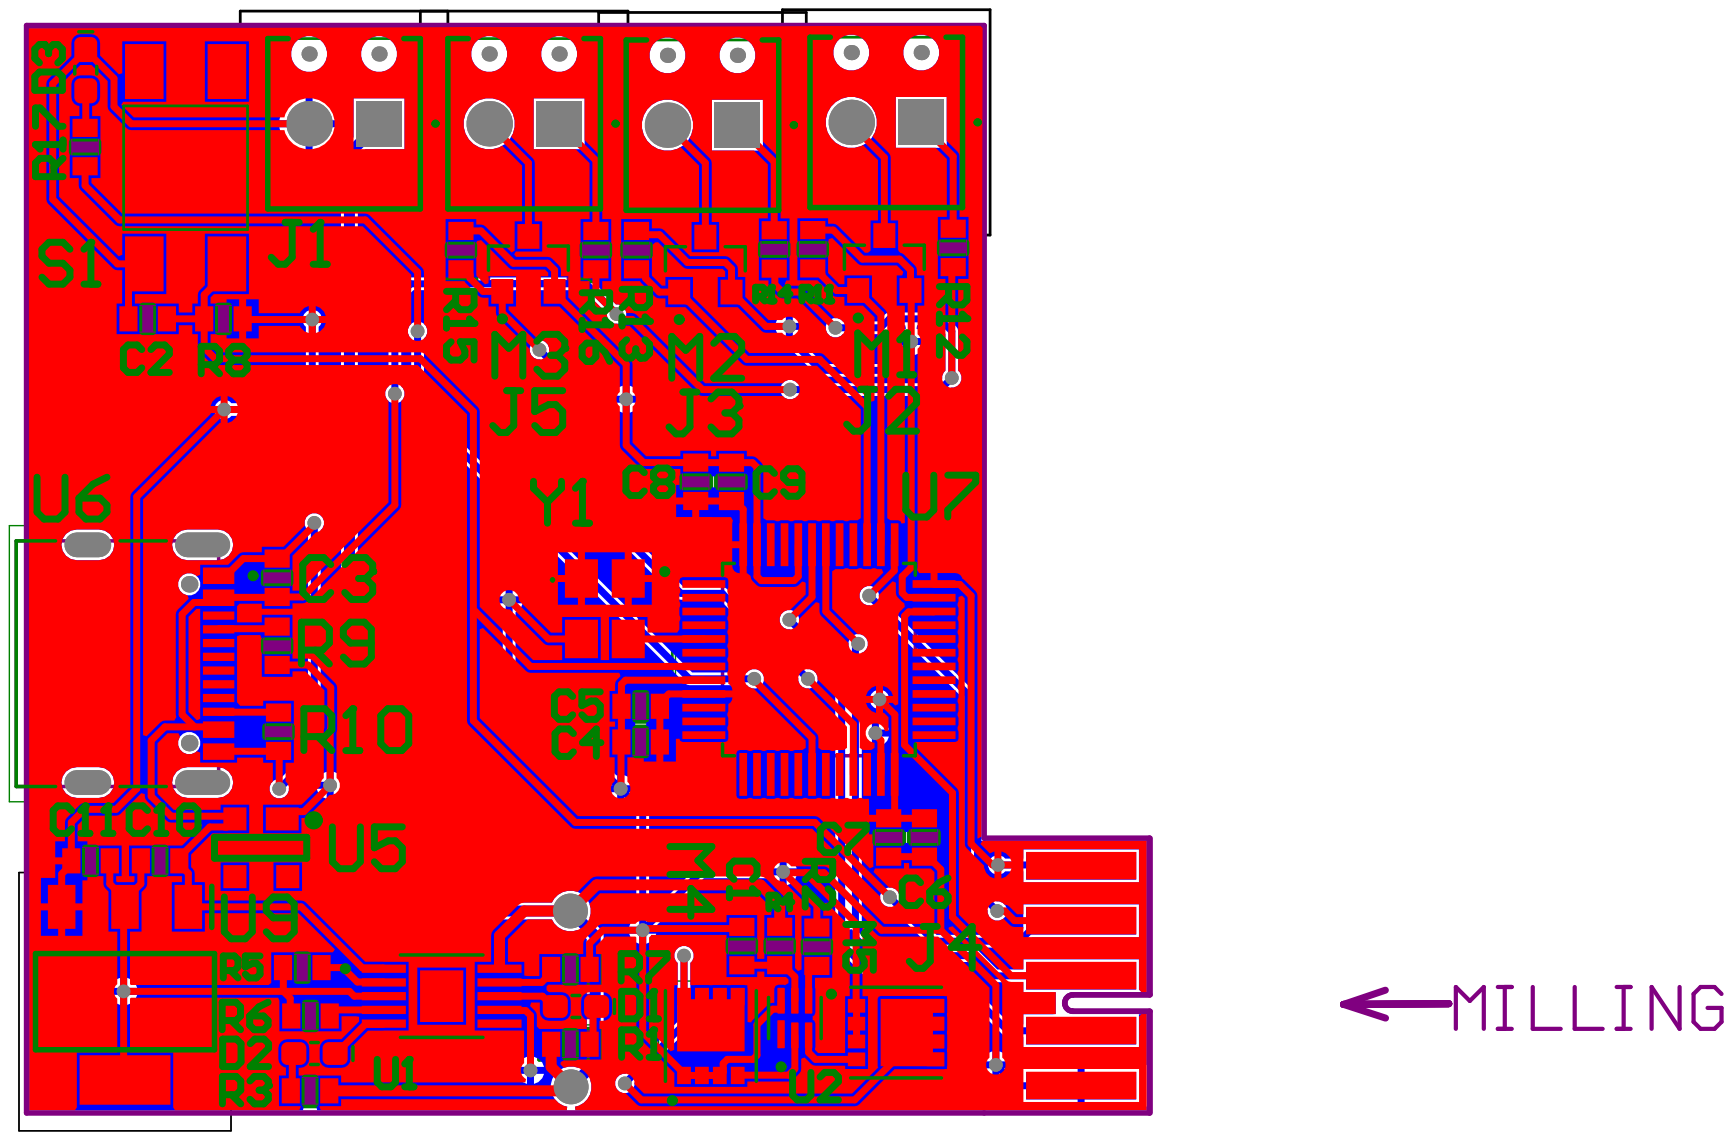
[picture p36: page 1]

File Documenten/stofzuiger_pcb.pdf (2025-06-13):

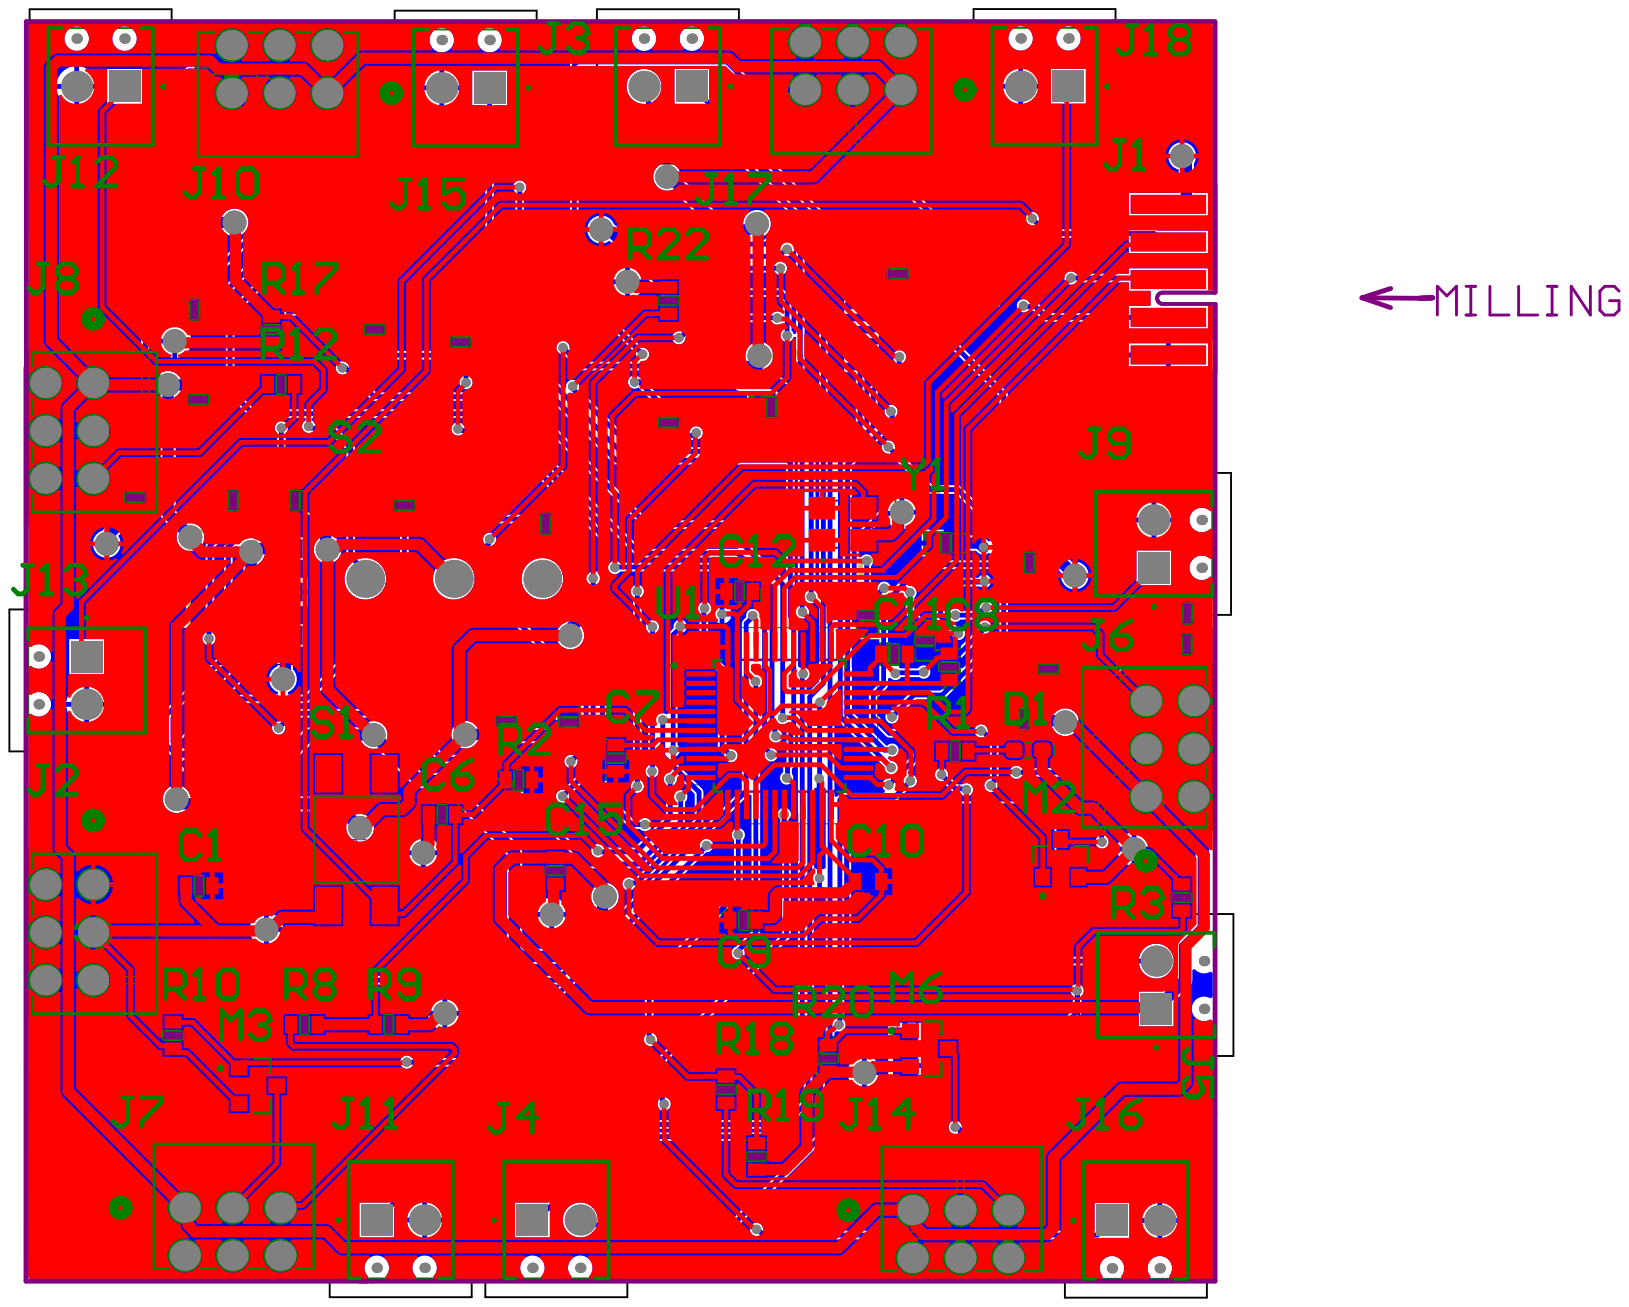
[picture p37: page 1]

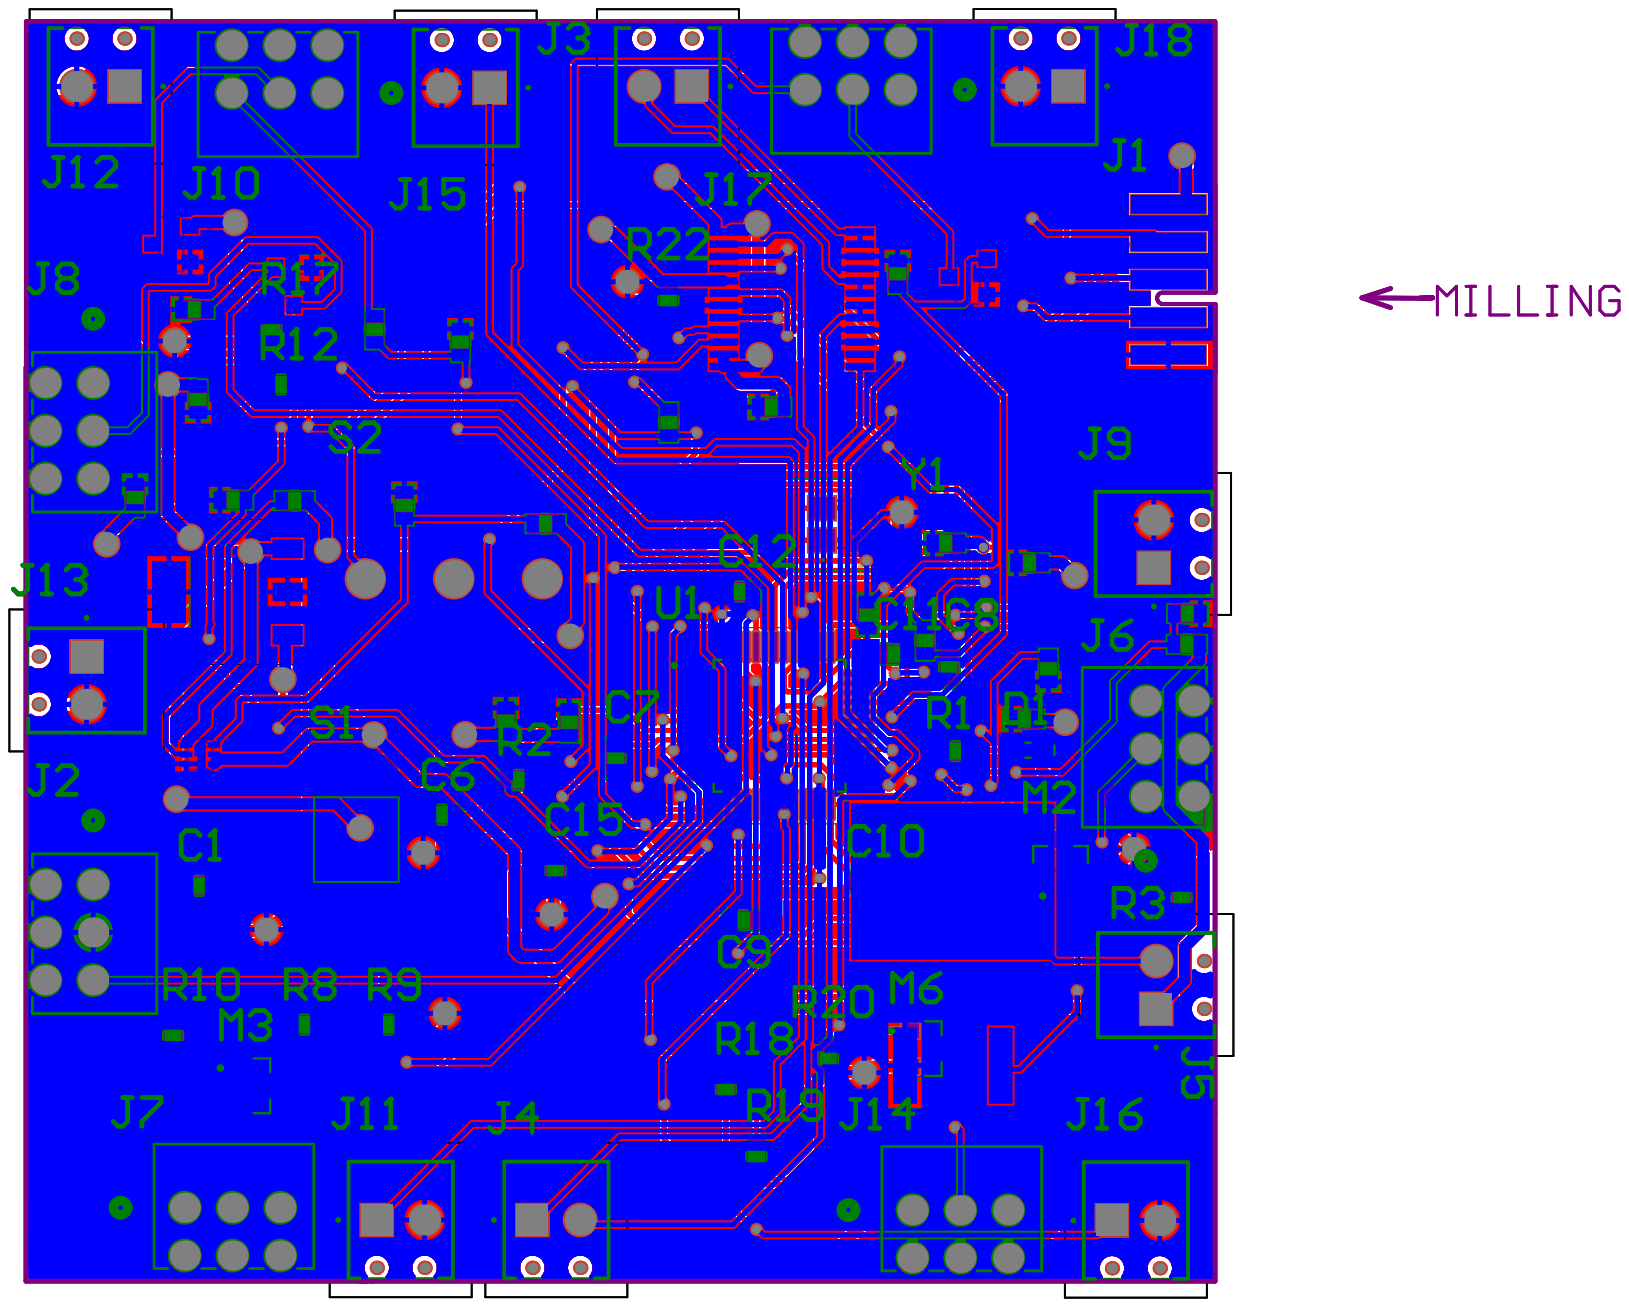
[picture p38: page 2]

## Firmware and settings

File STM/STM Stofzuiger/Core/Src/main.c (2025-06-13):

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
/* Includes ------------------------------------------------------------------*/
#include "main.h"

/* USER CODE BEGIN Includes */
#include <stdio.h>
/* USER CODE END Includes */

/* USER CODE BEGIN PM */
#define VOORUIT (GPIOB->BSRR = 0xF800B000);
#define ACHTERUIT (GPIOB->BSRR = 0xF8006800);
#define LINKS (GPIOB->BSRR = 0xF800A800);
#define RECHTS (GPIOB->BSRR = 0xF8007000);
#define UIT (GPIOB->BSRR = 0xF8000000);
#define NORMAL_SPEED 255
#define DOCK_SPEED 145
#define IR_SENSOR_COUNT 3
#define IR_SENSOR_DISTANCE 1500
#define IR_MID_SENSOR_DISTANCE 2200
#define ACHTERUIT_DELAY 500
#define DRAAI_DELAY 1500
#define LANG_DRAAI_DELAY 3000
/* USER CODE END PM */

ADC_HandleTypeDef hadc;

TIM_HandleTypeDef htim2;
TIM_HandleTypeDef htim6;

UART_HandleTypeDef huart1;

/* USER CODE BEGIN PV */
uint8_t sample = 0;
uint8_t data = 0;
uint8_t data_ready = 0;
uint8_t data_beacon = 0;
/* USER CODE END PV */

void SystemClock_Config(void);
static void MX_GPIO_Init(void);
static void MX_ADC_Init(void);
static void MX_TIM2_Init(void);
static void MX_USART1_UART_Init(void);
static void MX_TIM6_Init(void);
/* USER CODE BEGIN PFP */
int _write(int, char *, int);
void HAL_TIM_PeriodElapsedCallback (TIM_HandleTypeDef *);
void HAL_GPIO_EXTI_Callback(uint16_t);
void readAdc(uint32_t []);
uint8_t driveDock(uint8_t, uint32_t [], uint8_t *, uint8_t *);
void driveNormal(uint32_t []);
/* USER CODE END PFP */

/* USER CODE BEGIN 0 */
int _write(int file, char *ptr, int len) {
	for(int i = 0; i < len; i++){
		if(ptr[i]=='\n'){
			HAL_UART_Transmit(&huart1, (uint8_t*)"\r", 1, HAL_MAX_DELAY);
		}
		HAL_UART_Transmit(&huart1, (uint8_t*)&ptr[i], 1, HAL_MAX_DELAY);
	}
    return len;
}
void HAL_TIM_PeriodElapsedCallback (TIM_HandleTypeDef *htim)
{
	//HAL_GPIO_TogglePin(PIN_GPIO_Port, PIN_Pin);
	sample = !HAL_GPIO_ReadPin(IR_GPIO_Port, IR_Pin); //MSB eerst
	data = (data << 1) | sample; //actief lage pin => bit toggelen
	HAL_TIM_Base_Stop_IT(&htim6);
	__HAL_TIM_SET_COUNTER(&htim6, 0);
	if ((data == 0xa4) || (data == 0xa8) || (data == 0xac))
	{
		data_ready = data;
	}
	if (data == 0xa1)
	{
		data_beacon = data;
	}
}
void HAL_GPIO_EXTI_Callback(uint16_t IR_EXTI_IRQn)
{
	HAL_TIM_Base_Start_IT(&htim6);
}
void readAdc(uint32_t result[])
{
	ADC_ChannelConfTypeDef sConfig = {0};

	sConfig.Channel = ADC_CHANNEL_0;
	HAL_ADC_ConfigChannel(&hadc, &sConfig);
	HAL_ADC_Start(&hadc);
	HAL_ADC_PollForConversion(&hadc, 1);
	result[0] = HAL_ADC_GetValue(&hadc);

	sConfig.Channel = ADC_CHANNEL_1;
	HAL_ADC_ConfigChannel(&hadc, &sConfig);
	HAL_ADC_Start(&hadc);
	HAL_ADC_PollForConversion(&hadc, 1);
	result[2] = HAL_ADC_GetValue(&hadc);

	sConfig.Channel = ADC_CHANNEL_2;
	HAL_ADC_ConfigChannel(&hadc, &sConfig);
	HAL_ADC_Start(&hadc);
	HAL_ADC_PollForConversion(&hadc, 1);
	result[1] = HAL_ADC_GetValue(&hadc);

	printf("RECHTS: %ld, MIDDEN: %ld, LINKS: %ld\n", result[0], result[2], result[1]);
}
uint8_t driveDock(uint8_t state_dock, uint32_t adc_values[], uint8_t *drive_dock, uint8_t *detect_dock)
{
	switch (state_dock)
	{
	case 0:
		htim2.Instance->CCR1 = DOCK_SPEED; //Duty Cycle op 50% => led 38kHz
		htim2.Instance->CCR3 = DOCK_SPEED; //Duty Cycle op 50% => led 38kHz
		readAdc(adc_values);
		driveNormal(adc_values);

		if (data_ready == 0xac)
		{
			(*detect_dock)++;
		}

		if (*detect_dock == 1) //150 ms delay
		{
			state_dock = 1;
		}
		break;
	case 1:
		if (data_ready == 0xa4)
		{
			VOORUIT;
			htim2.Instance->CCR1 = 0; //Duty Cycle op 50% => led 38kHz
			htim2.Instance->CCR3 = DOCK_SPEED; //Duty Cycle op 50% => led 38kHz
		}
		else if (data_ready == 0xa8)
		{
			VOORUIT;
			htim2.Instance->CCR1 = DOCK_SPEED; //Duty Cycle op 50% => led 38kHz
			htim2.Instance->CCR3 = 0; //Duty Cycle op 50% => led 38kHz
		}
		else if (data_ready == 0xac)
		{
			VOORUIT;
			htim2.Instance->CCR1 = DOCK_SPEED; //Duty Cycle op 50% => led 38kHz
			htim2.Instance->CCR3 = DOCK_SPEED; //Duty Cycle op 50% => led 38kHz
		}

		readAdc(adc_values);
		if (adc_values[2] > IR_SENSOR_DISTANCE)
		{
			state_dock = 2;
		}
		break;
	case 2:
		UIT;
		data_ready = 0;
		data_beacon = 0;
		if (!HAL_GPIO_ReadPin(DRUK0_GPIO_Port, DRUK0_Pin))
		{
			while (!HAL_GPIO_ReadPin(DRUK0_GPIO_Port, DRUK0_Pin));
			ACHTERUIT;
			htim2.Instance->CCR1 = DOCK_SPEED; //Duty Cycle op 50% => led 38kHz
			htim2.Instance->CCR3 = DOCK_SPEED; //Duty Cycle op 50% => led 38kHz
			HAL_Delay(ACHTERUIT_DELAY);
			RECHTS;
			HAL_Delay(DRAAI_DELAY);
			*drive_dock = 0;
			*detect_dock = 0;
			state_dock = 0;
		}
		break;
	}
	return state_dock;
}
void driveNormal(uint32_t adc_values[])
{
	if (HAL_GPIO_ReadPin(DRUK4_GPIO_Port, DRUK4_Pin) == 0) //bumper links
	{
		ACHTERUIT;
		HAL_Delay(ACHTERUIT_DELAY);
		LINKS;
		HAL_Delay(DRAAI_DELAY);
	}
	else if (HAL_GPIO_ReadPin(DRUK2_GPIO_Port, DRUK2_Pin) == 0) //bumper rechts
	{
		ACHTERUIT;
		HAL_Delay(ACHTERUIT_DELAY);
		RECHTS;
		HAL_Delay(DRAAI_DELAY);
	}
	else if (HAL_GPIO_ReadPin(DRUK1_GPIO_Port, DRUK1_Pin) == 0) //bumper rechts
	{
		ACHTERUIT;
		HAL_Delay(ACHTERUIT_DELAY);
		LINKS;
		HAL_Delay(LANG_DRAAI_DELAY);
	}

	if (adc_values[0] > IR_SENSOR_DISTANCE && adc_values[1] < IR_SENSOR_DISTANCE)
	{
		LINKS;
		//VOORUIT;
		//htim2.Instance->CCR1 = NORMAL_SPEED; //Duty Cycle op 50% => led 38kHz
		//htim2.Instance->CCR3 = 0; //Duty Cycle op 50% => led 38kHz
	}
	else if (adc_values[1] > IR_SENSOR_DISTANCE && adc_values[0] < IR_SENSOR_DISTANCE)
	{
		RECHTS;
		//VOORUIT;
		//htim2.Instance->CCR1 = 0; //Duty Cycle op 50% => led 38kHz
		//htim2.Instance->CCR3 = NORMAL_SPEED; //Duty Cycle op 50% => led 38kHz
	}
	else if (adc_values[0] > IR_MID_SENSOR_DISTANCE && adc_values[1] > IR_MID_SENSOR_DISTANCE)
	{
		ACHTERUIT;
		HAL_Delay(ACHTERUIT_DELAY);
		if (adc_values[0] > adc_values[1])
		{
			LINKS;
			HAL_Delay(DRAAI_DELAY);
		}
		else
		{	RECHTS;
			HAL_Delay(DRAAI_DELAY);
		}
	}
	else if (adc_values[2] > IR_MID_SENSOR_DISTANCE)
	{
		ACHTERUIT;
		HAL_Delay(ACHTERUIT_DELAY);
		if (adc_values[0] > adc_values[1])
		{
			LINKS;
			HAL_Delay(DRAAI_DELAY);
		}
		else
		{
			RECHTS;
			HAL_Delay(DRAAI_DELAY);
		}
	}
	else
	{
		VOORUIT;
		//htim2.Instance->CCR1 = NORMAL_SPEED; //Duty Cycle op 50% => led 38kHz
		//htim2.Instance->CCR3 = NORMAL_SPEED; //Duty Cycle op 50% => led 38kHz
	}
}
/* USER CODE END 0 */

/**
  * @brief  The application entry point.
  * @retval int
  */
int main(void)
{

  /* USER CODE BEGIN 1 */
	uint32_t adc_values[IR_SENSOR_COUNT];
	uint8_t drive_dock = 0;
	uint8_t state_dock = 0;
	uint8_t detect_dock = 0;
  /* USER CODE END 1 */

  /* MCU Configuration--------------------------------------------------------*/

  /* Reset of all peripherals, Initializes the Flash interface and the Systick. */
  HAL_Init();

  /* Configure the system clock */
  SystemClock_Config();

  /* Initialize all configured peripherals */
  MX_GPIO_Init();
  MX_ADC_Init();
  MX_TIM2_Init();
  MX_USART1_UART_Init();
  MX_TIM6_Init();
  /* USER CODE BEGIN 2 */
  HAL_GPIO_WritePin(IR0_GPIO_Port, IR0_Pin, 1);
  HAL_GPIO_WritePin(IR1_GPIO_Port, IR1_Pin, 1);
  HAL_GPIO_WritePin(IR2_GPIO_Port, IR2_Pin, 1);
  HAL_TIM_PWM_Start(&htim2, TIM_CHANNEL_1);
  HAL_TIM_PWM_Start(&htim2, TIM_CHANNEL_3);
  HAL_Delay(50); //sensors moeten opstarten
  /* USER CODE END 2 */

  /* Infinite loop */
  /* USER CODE BEGIN WHILE */
  while (1)
  {
    /* USER CODE END WHILE */

    /* USER CODE BEGIN 3 */
	  switch (drive_dock)
	  {
	  case 0:
		  if (!HAL_GPIO_ReadPin(DRUK0_GPIO_Port, DRUK0_Pin))
		  {
			  while (!HAL_GPIO_ReadPin(DRUK0_GPIO_Port, DRUK0_Pin));
			  drive_dock ^= 1;
		  }
		  HAL_GPIO_WritePin(STOF_GPIO_Port, STOF_Pin, 1);
		  htim2.Instance->CCR1 = NORMAL_SPEED; //Duty Cycle op 50% => led 38kHz
		  htim2.Instance->CCR3 = NORMAL_SPEED; //Duty Cycle op 50% => led 38kHz
		  readAdc(adc_values);
		  printf("l: %d, m: %d, r: %d, ", HAL_GPIO_ReadPin(DRUK4_GPIO_Port, DRUK4_Pin), HAL_GPIO_ReadPin(DRUK1_GPIO_Port, DRUK1_Pin), HAL_GPIO_ReadPin(DRUK2_GPIO_Port, DRUK2_Pin));
		  driveNormal(adc_values);
		  break;
	  case 1:
		  HAL_GPIO_WritePin(STOF_GPIO_Port, STOF_Pin, 0);
		  printf("data: %x, %x, %d\n", data_ready, data_beacon, state_dock);
		  state_dock = driveDock(state_dock, adc_values, &drive_dock, &detect_dock);
		  break;
	  }
  }
  /* USER CODE END 3 */
}

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


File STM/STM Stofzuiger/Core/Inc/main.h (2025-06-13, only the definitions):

#define OSC_Pin GPIO_PIN_0
#define OSC_GPIO_Port GPIOH
#define STATUS_Pin GPIO_PIN_1
#define STATUS_GPIO_Port GPIOH
#define IR1_Pin GPIO_PIN_7
#define IR1_GPIO_Port GPIOA
#define DRUK5_Pin GPIO_PIN_0
#define DRUK5_GPIO_Port GPIOB
#define DRUK5_EXTI_IRQn EXTI0_1_IRQn
#define DRUK4_Pin GPIO_PIN_1
#define DRUK4_GPIO_Port GPIOB
#define DRUK4_EXTI_IRQn EXTI0_1_IRQn
#define DRUK3_Pin GPIO_PIN_2
#define DRUK3_GPIO_Port GPIOB
#define DRUK3_EXTI_IRQn EXTI2_3_IRQn
#define CH3_Pin GPIO_PIN_10
#define CH3_GPIO_Port GPIOB
#define BIN2_Pin GPIO_PIN_11
#define BIN2_GPIO_Port GPIOB
#define BIN1_Pin GPIO_PIN_12
#define BIN1_GPIO_Port GPIOB
#define STBY_Pin GPIO_PIN_13
#define STBY_GPIO_Port GPIOB
#define AIN2_Pin GPIO_PIN_14
#define AIN2_GPIO_Port GPIOB
#define AIN1_Pin GPIO_PIN_15
#define AIN1_GPIO_Port GPIOB
#define IR2_Pin GPIO_PIN_8
#define IR2_GPIO_Port GPIOA
#define IR3_Pin GPIO_PIN_9
#define IR3_GPIO_Port GPIOA
#define IR4_Pin GPIO_PIN_10
#define IR4_GPIO_Port GPIOA
#define IR5_Pin GPIO_PIN_11
#define IR5_GPIO_Port GPIOA
#define IR0_Pin GPIO_PIN_12
#define IR0_GPIO_Port GPIOA
#define CH1_Pin GPIO_PIN_15
#define CH1_GPIO_Port GPIOA
#define DRUK2_Pin GPIO_PIN_3
#define DRUK2_GPIO_Port GPIOB
#define DRUK2_EXTI_IRQn EXTI2_3_IRQn
#define DRUK1_Pin GPIO_PIN_4
#define DRUK1_GPIO_Port GPIOB
#define DRUK1_EXTI_IRQn EXTI4_15_IRQn
#define DRUK0_Pin GPIO_PIN_5
#define DRUK0_GPIO_Port GPIOB
#define TX_Pin GPIO_PIN_6
#define TX_GPIO_Port GPIOB
#define RX_Pin GPIO_PIN_7
#define RX_GPIO_Port GPIOB
#define IR_Pin GPIO_PIN_8
#define IR_GPIO_Port GPIOB
#define IR_EXTI_IRQn EXTI4_15_IRQn
#define STOF_Pin GPIO_PIN_9
#define STOF_GPIO_Port GPIOB

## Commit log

2025-03-07 pcb lib update
    [PcbLib1.PcbLib]
2025-03-07 stm project
    [PcbLib1.PcbLib, pxc_1725669_09_03_MPT-0-5-3-2-54_3D.stp]
2025-03-07 add designators
    [Schlib1.SchLib, Stofzuiger.SchDoc]
2025-03-07 schema aangepast en een beke in sch lib
    [PE2.PrjPcb, Schlib1.SchLib, Stofzuiger.SchDoc]
2025-03-13 stofzuiger schema
    [Schlib1.SchLib, Stofzuiger.SchDoc, Top.SchDoc]
2025-03-14 Battery management
    [Oplader.SchDoc, Schlib1.SchLib]
2025-03-21 ESD_IC+ USB
    [Laadstation.SchDoc, Stofzuiger.SchDoc]
2025-03-23 schema aangepast
    [Extra.SchDoc, Laadstation.SchDoc, Oplader.SchDoc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]
2025-03-24 sch lib
    [Oplader.SchDoc, PcbLib1.PcbLib, Schlib1.SchLib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]
2025-03-25 stmlink toegevoegd
    [7-Pin Header - Female - 2.54mm.step, Laadstation.SchDoc, PcbLib1.PcbLib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]
2025-03-25 uart aan
2025-03-28 voeding ontkoppeling
    [Laadstation.SchDoc, Oplader.SchDoc, Stofzuiger.SchDoc]
2025-03-28 bq fix
    [Oplader.SchDoc, Schlib1.SchLib]
2025-03-28 bq fixiixix
    [Oplader.SchDoc]
2025-03-28 pe2 laadstation n ieuw project
    [Oplader.SchDoc, Schlib1.SchLib]
2025-03-28 pcb toegevoegd
    [Laadstation.PcbDoc, Laadstation.SchDoc, Oplader.SchDoc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]
2025-04-04 pcb stofzuiger
2025-04-05 fabrication outputs
    [Extra.SchDoc, Laadstation.PcbDoc, PE2 laadstation.PrjPcb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]
2025-06-09 laatste update (alles)
    [009159010061916.stp]
2025-06-14 flowcharts verslag
2025-06-15 update flowchart
